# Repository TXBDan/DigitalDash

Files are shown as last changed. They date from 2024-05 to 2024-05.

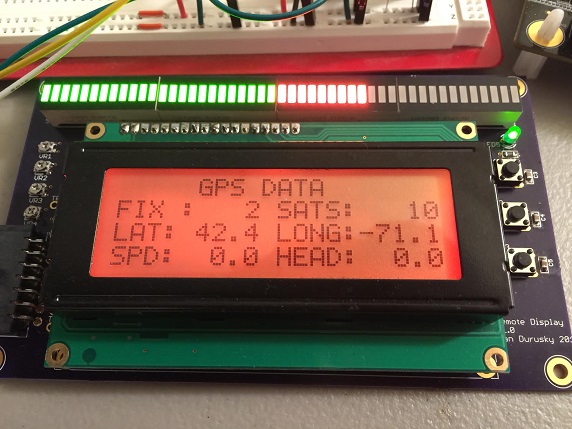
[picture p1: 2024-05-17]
pics/gpspic.jpg

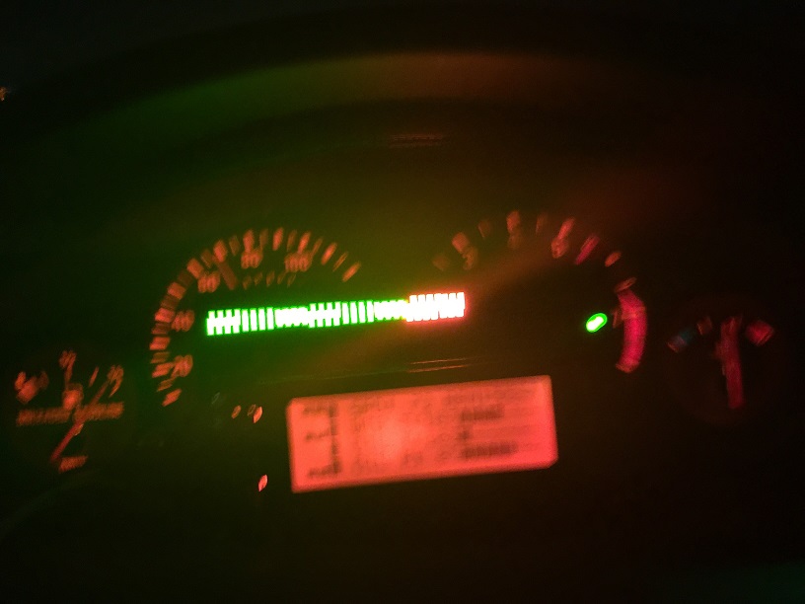
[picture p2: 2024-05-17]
pics/dashnight2.jpg

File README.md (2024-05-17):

# DigitalDash

This is a prototype digital dashboard for use in motorsports. I made it in 2015 and successfully ran it in my track car for a couple years. I'm now archiving the project here.

It features:
* LPC4088 microcontroller
* Many-LED RGB sequential shift light
* 20x4 character LCD display
* 2 LEDs (power/status and alarm)
* 3 push buttons (change screen, select, option)
* 4 analog inputs (water temp, oil temp, oil pressure, throttle position)
* 2 speed/pulse inputs (speed and tach)
* 10Hz GPS (position and elevation)
* 3-axis accelerometer
* SDcard logging

For a lot more info, check out the blog here: https://projectsofdan.com/?cat=18

incar

BlockDiagram

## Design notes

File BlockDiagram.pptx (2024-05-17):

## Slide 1

QSB Baseboard

Main Unit Shield

Dashboard

Shift Light 1-2
HT16K33
I2C1: 0x70

Shift Light 3-4
HT16K33
I2C1: 0x71

20x4 LCD
MCP2300
I2C1: 0x40

Power LED

8chan ADC
MCP3208
SPI1

Pull-up Jumpers

Input Filters

Input Buffers

Temp Sensor
AEM 30-2012

LPC4088
ARM Cortex M4

Temp Sensor
AEM 30-2012

Pressure Sensor
AEM 30-2131-100

Throttle Position
Stock Potentiometer

Trim Pot (R)

Record Button

Trim Pot (G)

Button 1

Accelerometer
MMA7455
I2C1

Vehicle Speed
12V pulse train

Trim Pot (B)

SD Memory Card

Engine Speed
12V pulse train

Trim Pot (Contrast)

Button 2

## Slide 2

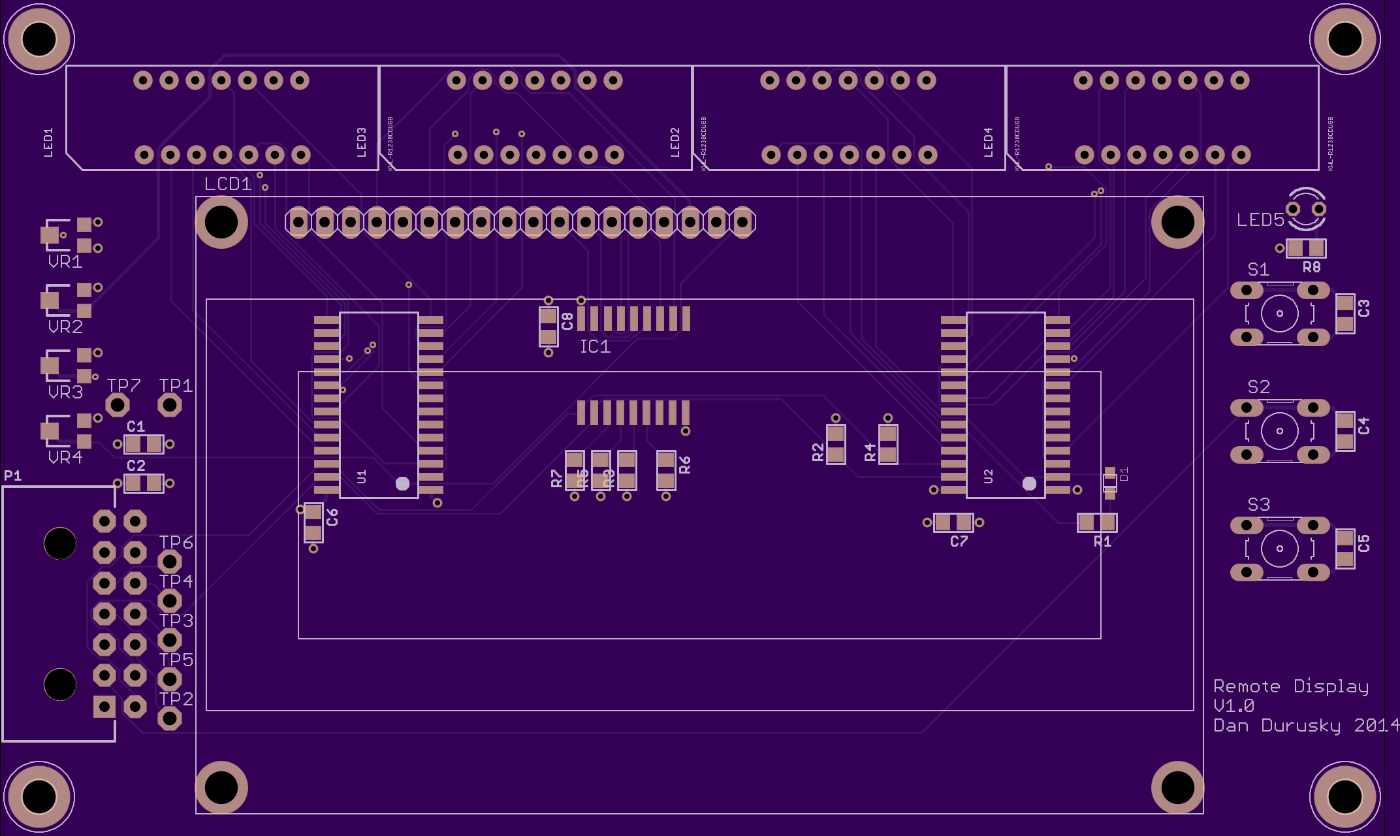
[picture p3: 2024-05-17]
hardware/RemoteDisplay/Layout/top.png

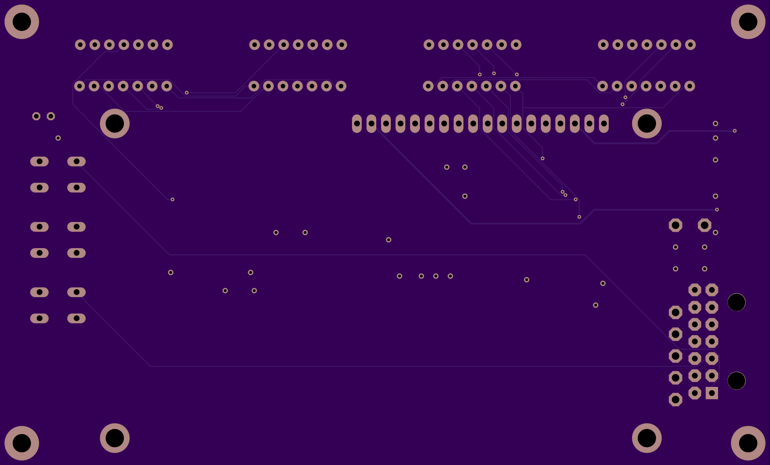
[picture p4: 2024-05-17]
hardware/RemoteDisplay/Layout/bottom.png

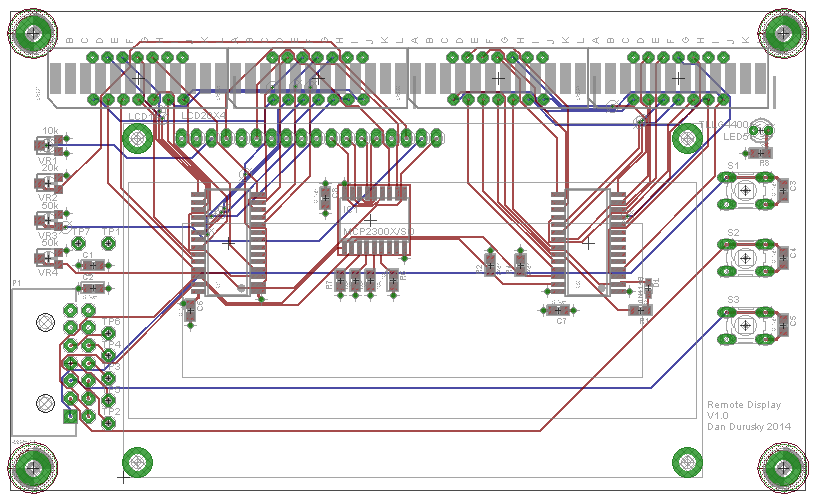
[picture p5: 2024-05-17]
hardware/RemoteDisplay/Layout/Layout.png

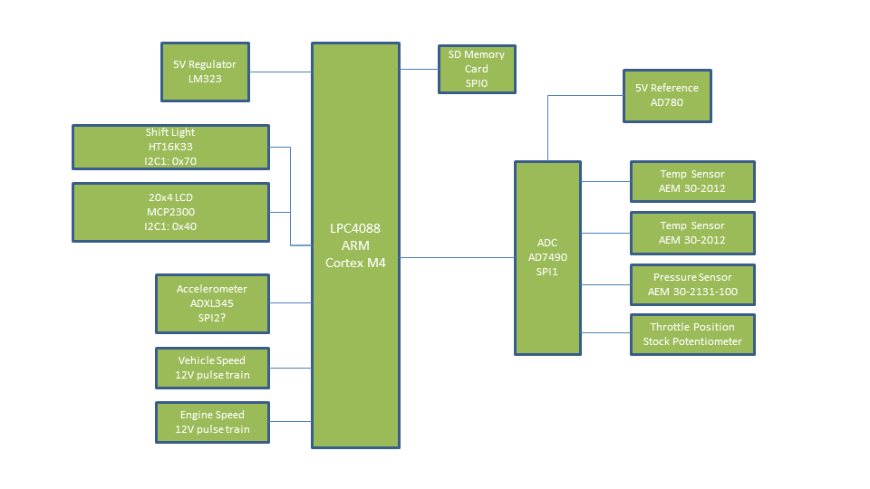
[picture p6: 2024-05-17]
BlockDiagram.png

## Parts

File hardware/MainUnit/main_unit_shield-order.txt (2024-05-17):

Order list for C:/Users/Dan/Documents/eagle/DigitalDash/main_unit_shield.sch					
Exported from EAGLE with DesignLink					
					
Quantity	Value	Package	Manufacturer	Manuf. PN	Description
11	0.1uF	C0805	TDK	C2012X7R1H104K085AA	"TDK - C2012X7R1H104K085AA - CERAMIC CAPACITOR, 0.1UF, 50V, X7R, 0805"
3	10uF	C0805	TDK	C2012X5R1E106K125AB	"TDK - C2012X5R1E106K125AB - CERAMIC CAPACITOR, 10UF, 25V, X5R, 0805"
4		JP1	3M	969102-0000-DA	"3M - 969102-0000-DA - SHUNT, 2POS, 2.54MM"
1	43045-24	43045-24	MOLEX	43045-2400	"MOLEX - 43045-2400 - PLUG & SOCKET CONNECTOR, HEADER, 24POS, 3MM"
1	43045-14	43045-14	MOLEX	43045-1400	"MOLEX - 43045-1400 - PLUG & SOCKET CONNECTOR, HEADER, 14POS, 3MM"
50			Molex	462350001	CONN SOCKET 20-24AWG GOLD
2	20k	R0805	VISHAY/DALE	CRCW080520K0FKEA	"VISHAY DALE - CRCW080520K0FKEA - THICK FILM RESISTOR, 20KOHM, 125mW, 1%"
14	2K2	R0805	VISHAY/DALE	CRCW08052K20FKEA	"VISHAY DALE - CRCW08052K20FKEA - THICK FILM RESISTOR, 2.2KOHM, 125mW, 1%"
2	8k2	R0805	VISHAY/DALE	CRCW08058K20FKEAHP	"VISHAY DRALORIC - CRCW08058K20FKEAHP - RESISTOR, POWER, 0805, 1%, 8K20"
3		SO14	MICROCHIP	MCP6044-E/SL	"MICROCHIP - MCP6044-E/SL - IC, OP-AMP, 14kHZ, 0.003V/ us, 3mV, SOIC14"
1		SO16	MICROCHIP	MCP3208-BI/SL	"MICROCHIP - MCP3208-BI/SL - IC, ADC 12BIT 100kSPS SERIAL SPI SOIC-16"

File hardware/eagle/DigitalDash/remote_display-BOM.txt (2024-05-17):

Order list for C:/Users/Dan/Documents/eagle/DigitalDash/remote_display.sch
Exported from EAGLE with DesignLink

Quantity	Value	Package	Order code	Manufacturer	Manuf. Code	Availability	Price (from)	Description
1	10uF	C0805	04X3278		C2012X5R1E106K125AB	8292	0.229	TDK - C2012X5R1E106K125AB - CERAMIC CAPACITOR, 10UF, 25V, X5R, 0805
7	0.1uF	C0805	04X3288		C2012X7R1H104K085AA	2978	0.016	TDK - C2012X7R1H104K085AA - CERAMIC CAPACITOR, 0.1UF, 50V, X7R, 0805
1	1N4148	SOD-323F	10N9478		MMBT2222ALT3G	4288	0.025	ON SEMICONDUCTOR - MMBT2222ALT3G - BIPOLAR TRANSISTOR, NPN, 40V SOT-23
4	MOUNT-PAD-ROUND3.2	3,2-PAD	unknown					
1	MCP2300X/SO	SO18W	08J8738	MICROCHIP	MCP23008-E/SO	305	0.78	MICROCHIP - MCP23008-E/SO - IC, I/O EXPANDER, 8BIT, 1.7MHZ, SOIC-18
1	LCD20X4	LCD20X4	unknown					
4	KWL-R1230CDUGB	SEGMENT_BICOL_BL-AR12Z3010	unknown					
1	TLLG4400	LED3MM	58K2496	VISHAY/TELEFUNKEN	TLLG4400	29708	0.095	VISHAY SEMICONDUCTOR - TLLG4400 - LED, GREEN, T-1 (3MM), 1.2MCD, 575NM
1	43045-14	43045-14	55R8852		43045-1400	471	2.1	MOLEX - 43045-1400 - PLUG & SOCKET CONNECTOR, HEADER, 14POS, 3MM
1	47k	R0805	41R4787		CRCW080547K0FKEAHP	4329	0.049	VISHAY DRALORIC - CRCW080547K0FKEAHP - RESISTOR, POWER, 0805, 1%, 47K0
2	DNP	R0805	05F1511	VISHAY/DALE	CRCW080510K0FKTA	6001	0.021	VISHAY DALE - CRCW080510K0FKTA - THICK FILM RESISTOR, 10KOHM, 125mW, 1%
4	10k	R0805	05F1511	VISHAY/DALE	CRCW080510K0FKTA	6001	0.021	VISHAY DALE - CRCW080510K0FKTA - THICK FILM RESISTOR, 10KOHM, 125mW, 1%
1	1K2	R0805	05F1511	VISHAY/DALE	CRCW080510K0FKTA	6001	0.021	VISHAY DALE - CRCW080510K0FKTA - THICK FILM RESISTOR, 10KOHM, 125mW, 1%
3		B3F-10XX	unknown		B3F-1000			
7	TPSPAD1-13	P1-13	unknown					
2		SOP28_300MIL	unknown					
1	10k	TC33X	60H9648	BOURNS, INC.	TC33X-2-103E	7500	0.094	BOURNS - TC33X-2-103E - TRIMMER POTENTIOMETER 10KOHM 1TURN, FULL REEL
1	20k	TC33X	97M3839		TC33X-2-203E	0		BOURNS - TC33X-2-203E - TRIMMER POTENTIOMETER 20KOHM -000TURN SMD
2	50k	TC33X	97M3841		TC33X-2-503E	4443	0.113	BOURNS - TC33X-2-503E - TRIMMER POTENTIOMETER 50KOHM -000TURN SMD

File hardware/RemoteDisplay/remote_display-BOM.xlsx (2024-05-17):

Order list for C:/Users/Dan/Documents/eagle/DigitalDash/remote_display.sch
Exported from EAGLE with DesignLink
Quantity | Value | Package | Manufacturer | Manuf. PN | Description
1 | 10uF | C0805 | TDK | C2012X5R1E106K125AB | TDK - C2012X5R1E106K125AB - CERAMIC CAPACITOR, 10UF, 25V, X5R, 0805
7 | 0.1uF | C0805 | TDK | C2012X7R1H104K085AA | TDK - C2012X7R1H104K085AA - CERAMIC CAPACITOR, 0.1UF, 50V, X7R, 0805
1 | 1N4148 | SOD-323F | On Semi | MMBT2222ALT3G | BIPOLAR TRANSISTOR, NPN, 40V SOT-23
1 | MCP2300X/SO | SO18W | MICROCHIP | MCP23008-E/SO | MICROCHIP - MCP23008-E/SO - IC, I/O EXPANDER, 8BIT, 1.7MHZ, SOIC-18
1 | LCD20X4 | LCD20X4 | Adafruit | 499 | Adafruit RGB 20x4 LCD
4 | KWL-R1230CDUGB | SEGMENT_BICOL_BL-AR12Z3010 | Adafruit | KWL-R1230CDUGB | 12bar LED
1 | TLLG4400 | LED3MM | VISHAY/TELEFUNKEN | TLLG4400 | VISHAY SEMICONDUCTOR - TLLG4400 - LED, GREEN, T-1 (3MM), 1.2MCD, 575NM
1 |  | 43045-14 | Molex | 43045-1400 | MOLEX - 43045-1400 - PLUG & SOCKET CONNECTOR, HEADER, 14POS, 3MM
20 |  |  | Molex | 462350001 | CONN SOCKET 20-24AWG GOLD
1 | 47k | R0805 | VISHAY | CRCW080547K0FKEAHP | VISHAY DRALORIC - CRCW080547K0FKEAHP - RESISTOR, POWER, 0805, 1%, 47K0
2 | DNP | R0805 | VISHAY | CRCW080510K0FKTA | VISHAY DALE - CRCW080510K0FKTA - THICK FILM RESISTOR, 10KOHM, 125mW, 1%
4 | 10k | R0805 | VISHAY | CRCW080510K0FKTA | VISHAY DALE - CRCW080510K0FKTA - THICK FILM RESISTOR, 10KOHM, 125mW, 1%
1 | 1K2 | R0805 | VISHAY | CRCW080510K0FKTA | VISHAY DALE - CRCW080510K0FKTA - THICK FILM RESISTOR, 10KOHM, 125mW, 1%
3 |  | B3F-10XX | Omron | B3F-1000 | tactile button switch 6mm
2 |  | SOP28_300MIL | Holtek | HTK1633 | SOIC-28 RAM Mapping 16*8 LED Controller Driver
1 | 10k | TC33X | BOURNS, INC. | TC33X-2-103E | BOURNS - TC33X-2-103E - TRIMMER POTENTIOMETER 10KOHM 1TURN, FULL REEL
1 | 20k | TC33X | BOURNS, INC. | TC33X-2-203E | BOURNS - TC33X-2-203E - TRIMMER POTENTIOMETER 20KOHM -000TURN SMD
2 | 50k | TC33X | BOURNS, INC. | TC33X-2-503E | BOURNS - TC33X-2-503E - TRIMMER POTENTIOMETER 50KOHM -000TURN SMD

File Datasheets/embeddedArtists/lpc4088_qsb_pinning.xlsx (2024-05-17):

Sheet: All pins
Pin Functionality | Pin Name | Edge connector pins | Display connector pins | Xbee connector pins | Usage | Comments
P0[0] / CAN_RD_1 / U3_TXD / I2C1_SDA / U0_TXD | p0_0 | 9
P0[1] / CAN_TD_1 / U3_RXD / I2C1_SCL / U0_RXD | p0_1 | 10
P0[2] / U0_TXD / U3_TXD | p0_2 | 42 |  |  | HDK UART0 TX
P0[3] / U0_RXD / U3_RXD | p0_3 | 41 |  |  | HDK UART0 RX
P0[4] / I2S_RX_SCK / CAN_RD_2 / T2_CAP_0 / unused / CMP_ROSC / unused / LCD_VD_0 | p0_4 | 34 | 1 |  | LCD_VD0 | Only used for 24-bit color depth
P0[5] / I2S_RX_WS / CAN_TD_2 / T2_CAP_1 / unused / CMP_RESET / unused / LCD_VD_1 | p0_5 | 33 | 2 |  | LCD_VD1 | Only used for 24-bit color depth
P0[6] / I2S_RX_SDA / SSP1_SSEL / T2_MAT_0 / U1_RTS / CMP_ROSC / unused / LCD_VD_8 | p0_6 | 14 | 16 |  | LCD_VD8 | Only used for 24-bit color depth
P0[7] / I2S_TX_SCK / SSP1_SCK / T2_MAT_1 / RTC_EV0 / CMP_VREF / unused / LCD_VD_9 | p0_7 | 13 | 17 |  | LCD_VD9 | Only used for 24-bit color depth
P0[8] / I2S_TX_WS / SSP1_MISO / T2_MAT_2 / RTC_EV1 / CMP1_IN3 / unused / LCD_VD_16 | p0_8 | 12 | 29 |  | LCD_VD16 | Only used for 24-bit color depth
P0[9] / I2S_TX_SDA / SSP1_MOSI / T2_MAT_3 / RTC_EV2 / CMP1_IN2 / unused / LCD_VD_17 | p0_9 | 11 | 30 |  | LCD_VD17 | Only used for 24-bit color depth
P0[10] / U2_TXD / I2C2_SDA / T3_MAT_0 / unused / unused / unused / LCD_VD_5 | p0_10 |  | 10 |  | LCD_VD5
P0[11] / U2_RXD / I2C2_SCL / T3_MAT_1 / unused / unused / unused / LCD_VD_10 | p0_11 |  | 18 |  | LCD_VD10
P0[13] / USB_UP_LED2 / SSP1_MOSI / ADC0_IN[7] | p0_13 |  |  |  | Controls mbed LED#2
P0[19] / U1_DSR / SD_CLK / I2C1_SDA / unused / unused / unused / LCD_VD_13 | p0_19 |  | 24 |  | LCD_VD13
P0[20] / U1_DTR / SD_CMD / I2C1_SCL / unused / unused / unused / LCD_VD_14 | p0_20 |  | 26 |  | LCD_VD14
P0[21] / U1_RI / SD_PWR / U4_OE / CAN_RD_1 / U4_CLK | p0_21 | 8
P0[23] / ADC0_IN[0] / I2S_RX_SCK / T3_CAP_0 | p0_23 | 15
P0[24] / ADC0_IN[1] / I2S_RX_WS / T3_CAP_1 | p0_24 | 16
P0[25] / ADC0_IN[2] / I2S_RX_SDA / U3_TXD | p0_25 | 17
P0[26] / ADC0_IN[3] / DAC_OUT / U3_RXD | p0_26 | 18
P0[27] / I2C0_SDA / USB_SDA1 | p0_27 |  | 54 |  | LCD I2C interface (I2C#0)
P0[28] / I2C0_SCL / USB_SCL1 | p0_28 |  | 55 |  | LCD I2C interface (I2C#0)
P0[29] / USB_D+1 / EINT_0 | p0_29 |  |  |  | USB Host interface
P0[30] / USB_D-1 / EINT_1 | p0_30 |  |  |  | USB Host interface
P0[31] / USB_D+2 | p0_31 | 35 |  |  | USB Device or external interface
USB_D-2 | usb_dm2 | 36 |  |  | USB Device or external interface
P1[2] / ENET_TXD[2] / SD_CLK / PWM0_1 | p1_2 | 30
P1[3] / ENET_TXD[3] / SD_CMD / PWM0_2 | p1_3 | 29
P1[5] / ENET_TX_ER / SD_PWR / PWM0_3 / CMP1_IN1 | p1_5 | 28
P1[6] / ENET_TX_CLK / SD_DAT_0 / PWM0_4 / CMP0_IN3 | p1_6 | 27
P1[7] / ENET_COL / SD_DAT_1 / PWM0_5 / CMP1_IN0 | p1_7 | 26
P1[11] / ENET_RXD_2 / SD_DAT_2 / PWM0_6 | p1_11 | 25
P1[12] / ENET_RXD_3 / SD_DAT_3 / PWM0_CAP_0 / CMP1_OUT | p1_12 | 24
P1[13] / ENET_RX_DV | p1_13 |  |  |  | Controls mbed LED#3
P1[18] / USB_UP_LED1 / PWM1_1 / T1_CAP_0 / unused / SSP1_MISO | p1_18 |  |  |  | Controls mbed LED#1
P1[20] / USB_TX_DP1 / PWM1_2 / QEI_PHA / MC_FB0 / SSP0_SCK / LCD_VD_6 / LCD_VD_10 | p1_20 | 7 |  |  |  | Note that SPI0 is also used by LCD interface
P1[21] / USB_TX_DM1 / PWM1_3 / SSP0_SSEL / MC_ABORTn / unused / LCD_VD_7 / LCD_VD_11 | p1_21 |  | 20 |  | LCD_VD11
P1[22] / USB_RCV1 / USB_PWRD1 / T1_MAT_0 / MC_0B / SSP1_MOSI / LCD_VD_8 / LCD_VD_12 | p1_22 |  | 22 |  | LCD_VD12
P1[23] / USB_RX_DP1 / PWM1_4 / QEI_PHB / MC_FB1 / SSP0_MISO / LCD_VD_9 / LCD_VD_13 | p1_23 | 6 |  |  |  | Note that SPI0 is also used by LCD interface
P1[24] / USB_RX_DM1 / PWM1_5 / QEI_IDX / MC_FB2 / SSP0_MOSI / LCD_VD_10 / LCD_VD_14 | p1_24 | 5 |  |  |  | Note that SPI0 is also used by LCD interface
P1[25] / USB_LS1n / USB_HSTEN1n / T1_MAT_1 / MC_1A / CLKOUT / LCD_VD_11 / LCD_VD_15 | p1_25 |  | 28 |  | LCD_VD15
P1[26] / USB_SSPND1n / PWM1_6 / T0_CAP_0 / MC_1B / SSP1_SSEL / LCD_VD_12 / LCD_VD_20 | p1_26 |  | 36 |  | LCD_VD20
P1[27] / USB_INT1n / USB_OVRCR1n / T0_CAP_1 / CLKOUT / unused / LCD_VD_13 / LCD_VD_21 | p1_27 |  | 38 |  | LCD_VD21
P1[28] / USB_SCL1 / PWM1_CAP_0 / T0_MAT_0 / MC_2A / SSP0_SSEL / LCD_VD_14 / LCD_VD_22 | p1_28 |  | 40 |  | LCD_VD22
P1[29] / USB_SDA1 / PWM1_CAP_1 / T0_MAT_1 / MC_2B / U4_TXD / LCD_VD_15 / LCD_VD_23 | p1_29 |  | 42 |  | LCD_VD23
P1[30] / USB_PWRD2 / USB_VBUS / ADC0_IN[4] / I2C0_SDA / U3_OE | p1_30 | 19
P1[31] / USB_OVRCR2n / SSP1_SCK / ADC0_IN[5] / I2C0_SCL | p1_31 | 20
P2[0] / PWM1_1 / U1_TXD / unused / unused / unused / unused / LCD_PWR | p2_0 |  | 49 |  | LCD PWR
P2[1] / PWM1_2 / U1_RXD / unused / unused / unused / unused / LCD_LE | p2_1 |  | 53 |  | LCD LE
P2[2] / PWM1_3 / U1_CTS / T2_MAT_3 / unused / TRACEDATA[3] / unused / LCD_DCLK | p2_2 |  | 46 |  | LCD DCLK | Also used for trace data3
P2[3] / PWM1_4 / U1_DCD / T2_MAT_2 / unused / TRACEDATA[2] / unused / LCD_FP | p2_3 |  | 50 |  | LCD VSYNC | Also used for trace data2
P2[4] / PWM1_5 / U1_DSR / T2_MAT_1 / unused / TRACEDATA[1] / unused / LCD_ENAB_M | p2_4 |  | 48 |  | LCD DNAB | Also used for trace data1
P2[5] / PWM1_6 / U1_DTR / T2_MAT_0 / unused / TRACEDATA[0] / unused / LCD_LP | p2_5 |  | 52 |  | LCD HSYNC | Also used for trace data0
P2[6] / PWM1_CAP_0 / U1_RI / T2_CAP_0 / U2_OE / TRACECLK / LCD_VD_0 / LCD_VD_4 | p2_6 |  | 8 |  | LCD_VD4 | Also used for trace clock
P2[8] / CAN_TD_2 / U2_TXD / U1_CTS / ENET_MDC / unused / LCD_VD_2 / LCD_VD_6 | p2_8 |  | 12 |  | LCD_VD6
P2[9] / USB_CONNECT1 / U2_RXD / U4_RXD / ENET_MDIO / unused / LCD_VD_3 / LCD_VD_7 | p2_9 |  | 14 |  | LCD_VD7
P2[10] / EINT_0 / NMI | p2_10 | 23 |  |  |  | Must not be pulled low at reset, will enable ISP
P2[11] / EINT_1 / SD_DAT_1 / I2S_TX_SCK / unused / unused / unused / LCD_CLKIN | p2_11 |  | 44 |  | LCD CLKIN
P2[12] / EINT_2 / SD_DAT_2 / I2S_TX_WS / LCD_VD_4 / LCD_VD_3 / LCD_VD_8 / LCD_VD_18 | p2_12 |  | 32 |  | LCD_VD18
P2[13] / EINT_3 / SD_DAT_3 / I2S_TX_SDA / unused / LCD_VD_5 / LCD_VD_9 / LCD_VD_19 | p2_13 |  | 34 |  | LCD_VD19
P2[19] / EMC_CLK[1] | p2_19 |  |  |  | Controls mbed LED#4
P2[21] / EMC_DYCSn[1] | p2_21 |  | 60 |  | LCD GPIO
P2[22] / EMC_DYCSn[2] / SSP0_SCK / T3_CAP_0 | p2_22 |  | 56 |  | LCD SPI-SCK, using SPI0 | Signal can also exist at edge connector pin 7
P2[23] / EMC_DYCSn[3] / SSP0_SSEL / T3_CAP_1 | p2_23 |  | 57 |  | LCD SPI-SSEL,using SPI0
P2[25] / EMC_CKE[1] | p2_25 |  | 61 |  | LCD GPIO
P2[26] / EMC_CKE[2] / SSP0_MISO / T3_MAT_0 | p2_26 |  | 58 |  | LCD SPI-MISO, using SPI0 | Signal can also exist at edge connector pin 6
P2[27] / EMC_CKE[3] / SSP0_MOSI / T3_MAT_1 | p2_27 |  | 59 |  | LCD SPI-MOSI, using SPI0 | Signal can also exist at edge connector pin 5
P4[17] / EMC_A[17] | p4_17 |  |  | 5 | Xbee RESET
P4[18] / EMC_A[18] | p4_18 |  |  | 4 | Xbee CD/DOUT_EN
P4[19] / EMC_A[19] | p4_19 |  |  | 9 | Xbee DTR/SLEEP_RQ
P4[20] / EMC_A[20] / I2C2_SDA / SSP1_SCK | p4_20 |  |  | 12 | Xbee CTS
P4[21] / EMC_A[21] / I2C2_SCL / SSP1_SSEL | p4_21 |  |  | 16 | Xbee RTS
P4[22] / EMC_A[22] / U2_TXD / SSP1_MISO | p4_22 |  |  | 3 | Xbee DIN, using UART2
P4[23] / EMC_A[23] / U2_RXD / SSP1_MOSI | p4_23 |  |  | 2 | Xbee DOUT, using UART2
P4[28] / EMC_BLSn[2] / U3_TXD / T2_MAT_0 / unused / LCD_VD_6 / LCD_VD_10 / LCD_VD_2 | p4_28 |  | 4 |  | LCD_VD2
P4[29] / EMC_BLSn[3] / U3_RXD / T2_MAT_1 / I2C2_SCL / LCD_VD_7 / LCD_VD_11 / LCD_VD_3 | p4_29 |  | 6 |  | LCD_VD3
P5[0] / EMC_A[24] / SSP2_MOSI / T2_MAT_2 | p5_0 | 39
P5[1] / EMC_A[25] / SSP2_MISO / T2_MAT_3 | p5_1 | 38
P5[2] / EMC_A[26] / SSP2_SCK / T3_MAT_2 / unused / I2C0_SDA | p5_2 | 32 |  |  |  | Note that I2C0 is also used by LCD interface
P5[3] / EMC_A[27] / SSP2_SSEL / unused / U4_RXD / I2C0_SCL | p5_3 | 31 |  |  |  | Note that I2C0 is also used by LCD interface
P5[4] / U0_OE / unused / T3_MAT_3 / U4_TXD | p5_4 | 37
RESETn | resetn | 4
RTC_ALARM | rtc_alarm | 40
Vbat | vbat | 3

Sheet: Edge pins sorted
Pin Functionality | Pin Name | Edge connector pins | Display connector pins | Xbee connector pins | Usage | Comments
Vbat | vbat | 3
RESETn | resetn | 4
P1[24] / USB_RX_DM1 / PWM1_5 / QEI_IDX / MC_FB2 / SSP0_MOSI / LCD_VD_10 / LCD_VD_14 | p1_24 | 5 |  |  |  | Note that SPI0 is also used by LCD interface
P1[23] / USB_RX_DP1 / PWM1_4 / QEI_PHB / MC_FB1 / SSP0_MISO / LCD_VD_9 / LCD_VD_13 | p1_23 | 6 |  |  |  | Note that SPI0 is also used by LCD interface
P1[20] / USB_TX_DP1 / PWM1_2 / QEI_PHA / MC_FB0 / SSP0_SCK / LCD_VD_6 / LCD_VD_10 | p1_20 | 7 |  |  |  | Note that SPI0 is also used by LCD interface
P0[21] / U1_RI / SD_PWR / U4_OE / CAN_RD_1 / U4_CLK | p0_21 | 8
P0[0] / CAN_RD_1 / U3_TXD / I2C1_SDA / U0_TXD | p0_0 | 9
P0[1] / CAN_TD_1 / U3_RXD / I2C1_SCL / U0_RXD | p0_1 | 10
P0[9] / I2S_TX_SDA / SSP1_MOSI / T2_MAT_3 / RTC_EV2 / CMP1_IN2 / unused / LCD_VD_17 | p0_9 | 11 | 30 |  | LCD_VD17 | Only used for 24-bit color depth
P0[8] / I2S_TX_WS / SSP1_MISO / T2_MAT_2 / RTC_EV1 / CMP1_IN3 / unused / LCD_VD_16 | p0_8 | 12 | 29 |  | LCD_VD16 | Only used for 24-bit color depth
P0[7] / I2S_TX_SCK / SSP1_SCK / T2_MAT_1 / RTC_EV0 / CMP_VREF / unused / LCD_VD_9 | p0_7 | 13 | 17 |  | LCD_VD9 | Only used for 24-bit color depth
P0[6] / I2S_RX_SDA / SSP1_SSEL / T2_MAT_0 / U1_RTS / CMP_ROSC / unused / LCD_VD_8 | p0_6 | 14 | 16 |  | LCD_VD8 | Only used for 24-bit color depth
P0[23] / ADC0_IN[0] / I2S_RX_SCK / T3_CAP_0 | p0_23 | 15
P0[24] / ADC0_IN[1] / I2S_RX_WS / T3_CAP_1 | p0_24 | 16
P0[25] / ADC0_IN[2] / I2S_RX_SDA / U3_TXD | p0_25 | 17
P0[26] / ADC0_IN[3] / DAC_OUT / U3_RXD | p0_26 | 18
P1[30] / USB_PWRD2 / USB_VBUS / ADC0_IN[4] / I2C0_SDA / U3_OE | p1_30 | 19
P1[31] / USB_OVRCR2n / SSP1_SCK / ADC0_IN[5] / I2C0_SCL | p1_31 | 20
P2[10] / EINT_0 / NMI | p2_10 | 23 |  |  |  | Must not be pulled low at reset, will enable ISP
P1[12] / ENET_RXD_3 / SD_DAT_3 / PWM0_CAP_0 / CMP1_OUT | p1_12 | 24
P1[11] / ENET_RXD_2 / SD_DAT_2 / PWM0_6 | p1_11 | 25
P1[7] / ENET_COL / SD_DAT_1 / PWM0_5 / CMP1_IN0 | p1_7 | 26
P1[6] / ENET_TX_CLK / SD_DAT_0 / PWM0_4 / CMP0_IN3 | p1_6 | 27
P1[5] / ENET_TX_ER / SD_PWR / PWM0_3 / CMP1_IN1 | p1_5 | 28
P1[3] / ENET_TXD[3] / SD_CMD / PWM0_2 | p1_3 | 29
P1[2] / ENET_TXD[2] / SD_CLK / PWM0_1 | p1_2 | 30
P5[3] / EMC_A[27] / SSP2_SSEL / unused / U4_RXD / I2C0_SCL | p5_3 | 31 |  |  |  | Note that I2C0 is also used by LCD interface
P5[2] / EMC_A[26] / SSP2_SCK / T3_MAT_2 / unused / I2C0_SDA | p5_2 | 32 |  |  |  | Note that I2C0 is also used by LCD interface
P0[5] / I2S_RX_WS / CAN_TD_2 / T2_CAP_1 / unused / CMP_RESET / unused / LCD_VD_1 | p0_5 | 33 | 2 |  | LCD_VD1 | Only used for 24-bit color depth
P0[4] / I2S_RX_SCK / CAN_RD_2 / T2_CAP_0 / unused / CMP_ROSC / unused / LCD_VD_0 | p0_4 | 34 | 1 |  | LCD_VD0 | Only used for 24-bit color depth
P0[31] / USB_D+2 | p0_31 | 35 |  |  | USB Device or external interface
USB_D-2 | usb_dm2 | 36 |  |  | USB Device or external interface
P5[4] / U0_OE / unused / T3_MAT_3 / U4_TXD | p5_4 | 37
P5[1] / EMC_A[25] / SSP2_MISO / T2_MAT_3 | p5_1 | 38
P5[0] / EMC_A[24] / SSP2_MOSI / T2_MAT_2 | p5_0 | 39
RTC_ALARM | rtc_alarm | 40
P0[3] / U0_RXD / U3_RXD | p0_3 | 41 |  |  | HDK UART RX
P0[2] / U0_TXD / U3_TXD | p0_2 | 42 |  |  | HDK UART TX
P0[10] / U2_TXD / I2C2_SDA / T3_MAT_0 / unused / unused / unused / LCD_VD_5 | p0_10 |  | 10 |  | LCD_VD5
P0[11] / U2_RXD / I2C2_SCL / T3_MAT_1 / unused / unused / unused / LCD_VD_10 | p0_11 |  | 18 |  | LCD_VD10
P0[13] / USB_UP_LED2 / SSP1_MOSI / ADC0_IN[7] | p0_13 |  |  |  | Controls mbed LED#2
P0[19] / U1_DSR / SD_CLK / I2C1_SDA / unused / unused / unused / LCD_VD_13 | p0_19 |  | 24 |  | LCD_VD13
P0[20] / U1_DTR / SD_CMD / I2C1_SCL / unused / unused / unused / LCD_VD_14 | p0_20 |  | 26 |  | LCD_VD14
P0[27] / I2C0_SDA / USB_SDA1 | p0_27 |  | 54 |  | LCD I2C interface (I2C#0)
P0[28] / I2C0_SCL / USB_SCL1 | p0_28 |  | 55 |  | LCD I2C interface (I2C#0)
P0[29] / USB_D+1 / EINT_0 | p0_29 |  |  |  | USB Host interface
P0[30] / USB_D-1 / EINT_1 | p0_30 |  |  |  | USB Host interface
P1[13] / ENET_RX_DV | p1_13 |  |  |  | Controls mbed LED#3
P1[18] / USB_UP_LED1 / PWM1_1 / T1_CAP_0 / unused / SSP1_MISO | p1_18 |  |  |  | Controls mbed LED#1
P1[21] / USB_TX_DM1 / PWM1_3 / SSP0_SSEL / MC_ABORTn / unused / LCD_VD_7 / LCD_VD_11 | p1_21 |  | 20 |  | LCD_VD11
P1[22] / USB_RCV1 / USB_PWRD1 / T1_MAT_0 / MC_0B / SSP1_MOSI / LCD_VD_8 / LCD_VD_12 | p1_22 |  | 22 |  | LCD_VD12
P1[25] / USB_LS1n / USB_HSTEN1n / T1_MAT_1 / MC_1A / CLKOUT / LCD_VD_11 / LCD_VD_15 | p1_25 |  | 28 |  | LCD_VD15
P1[26] / USB_SSPND1n / PWM1_6 / T0_CAP_0 / MC_1B / SSP1_SSEL / LCD_VD_12 / LCD_VD_20 | p1_26 |  | 36 |  | LCD_VD20
P1[27] / USB_INT1n / USB_OVRCR1n / T0_CAP_1 / CLKOUT / unused / LCD_VD_13 / LCD_VD_21 | p1_27 |  | 38 |  | LCD_VD21
P1[28] / USB_SCL1 / PWM1_CAP_0 / T0_MAT_0 / MC_2A / SSP0_SSEL / LCD_VD_14 / LCD_VD_22 | p1_28 |  | 40 |  | LCD_VD22
P1[29] / USB_SDA1 / PWM1_CAP_1 / T0_MAT_1 / MC_2B / U4_TXD / LCD_VD_15 / LCD_VD_23 | p1_29 |  | 42 |  | LCD_VD23
P2[0] / PWM1_1 / U1_TXD / unused / unused / unused / unused / LCD_PWR | p2_0 |  | 49 |  | LCD PWR
P2[1] / PWM1_2 / U1_RXD / unused / unused / unused / unused / LCD_LE | p2_1 |  | 53 |  | LCD LE
P2[2] / PWM1_3 / U1_CTS / T2_MAT_3 / unused / TRACEDATA[3] / unused / LCD_DCLK | p2_2 |  | 46 |  | LCD DCLK | Also used for trace data3
P2[3] / PWM1_4 / U1_DCD / T2_MAT_2 / unused / TRACEDATA[2] / unused / LCD_FP | p2_3 |  | 50 |  | LCD VSYNC | Also used for trace data2
P2[4] / PWM1_5 / U1_DSR / T2_MAT_1 / unused / TRACEDATA[1] / unused / LCD_ENAB_M | p2_4 |  | 48 |  | LCD DNAB | Also used for trace data1
P2[5] / PWM1_6 / U1_DTR / T2_MAT_0 / unused / TRACEDATA[0] / unused / LCD_LP | p2_5 |  | 52 |  | LCD HSYNC | Also used for trace data0
P2[6] / PWM1_CAP_0 / U1_RI / T2_CAP_0 / U2_OE / TRACECLK / LCD_VD_0 / LCD_VD_4 | p2_6 |  | 8 |  | LCD_VD4 | Also used for trace clock
P2[8] / CAN_TD_2 / U2_TXD / U1_CTS / ENET_MDC / unused / LCD_VD_2 / LCD_VD_6 | p2_8 |  | 12 |  | LCD_VD6
P2[9] / USB_CONNECT1 / U2_RXD / U4_RXD / ENET_MDIO / unused / LCD_VD_3 / LCD_VD_7 | p2_9 |  | 14 |  | LCD_VD7
P2[11] / EINT_1 / SD_DAT_1 / I2S_TX_SCK / unused / unused / unused / LCD_CLKIN | p2_11 |  | 44 |  | LCD CLKIN
P2[12] / EINT_2 / SD_DAT_2 / I2S_TX_WS / LCD_VD_4 / LCD_VD_3 / LCD_VD_8 / LCD_VD_18 | p2_12 |  | 32 |  | LCD_VD18
P2[13] / EINT_3 / SD_DAT_3 / I2S_TX_SDA / unused / LCD_VD_5 / LCD_VD_9 / LCD_VD_19 | p2_13 |  | 34 |  | LCD_VD19
P2[19] / EMC_CLK[1] | p2_19 |  |  |  | Controls mbed LED#4
P2[21] / EMC_DYCSn[1] | p2_21 |  | 60 |  | LCD GPIO
P2[22] / EMC_DYCSn[2] / SSP0_SCK / T3_CAP_0 | p2_22 |  | 56 |  | LCD SPI-SCK, using SPI0 | Signal can also exist at edge connector pin 7
P2[23] / EMC_DYCSn[3] / SSP0_SSEL / T3_CAP_1 | p2_23 |  | 57 |  | LCD SPI-SSEL,using SPI0
P2[25] / EMC_CKE[1] | p2_25 |  | 61 |  | LCD GPIO
P2[26] / EMC_CKE[2] / SSP0_MISO / T3_MAT_0 | p2_26 |  | 58 |  | LCD SPI-MISO, using SPI0 | Signal can also exist at edge connector pin 6
P2[27] / EMC_CKE[3] / SSP0_MOSI / T3_MAT_1 | p2_27 |  | 59 |  | LCD SPI-MOSI, using SPI0 | Signal can also exist at edge connector pin 5
P4[17] / EMC_A[17] | p4_17 |  |  | 5 | Xbee RESET
P4[18] / EMC_A[18] | p4_18 |  |  | 4 | Xbee CD/DOUT_EN
P4[19] / EMC_A[19] | p4_19 |  |  | 9 | Xbee DTR/SLEEP_RQ
P4[20] / EMC_A[20] / I2C2_SDA / SSP1_SCK | p4_20 |  |  | 12 | Xbee CTS
P4[21] / EMC_A[21] / I2C2_SCL / SSP1_SSEL | p4_21 |  |  | 16 | Xbee RTS
P4[22] / EMC_A[22] / U2_TXD / SSP1_MISO | p4_22 |  |  | 3 | Xbee DIN, using UART2
P4[23] / EMC_A[23] / U2_RXD / SSP1_MOSI | p4_23 |  |  | 2 | Xbee DOUT, using UART2
P4[28] / EMC_BLSn[2] / U3_TXD / T2_MAT_0 / unused / LCD_VD_6 / LCD_VD_10 / LCD_VD_2 | p4_28 |  | 4 |  | LCD_VD2
P4[29] / EMC_BLSn[3] / U3_RXD / T2_MAT_1 / I2C2_SCL / LCD_VD_7 / LCD_VD_11 / LCD_VD_3 | p4_29 |  | 6 |  | LCD_VD3

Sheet: LCD pins sorted
Pin Functionality | Pin Name | Edge connector pins | Display connector pins | Xbee connector pins | Usage | Comments
P0[4] / I2S_RX_SCK / CAN_RD_2 / T2_CAP_0 / unused / CMP_ROSC / unused / LCD_VD_0 | p0_4 | 34 | 1 |  | LCD_VD0 | Only used for 24-bit color depth
P0[5] / I2S_RX_WS / CAN_TD_2 / T2_CAP_1 / unused / CMP_RESET / unused / LCD_VD_1 | p0_5 | 33 | 2 |  | LCD_VD1 | Only used for 24-bit color depth
P4[28] / EMC_BLSn[2] / U3_TXD / T2_MAT_0 / unused / LCD_VD_6 / LCD_VD_10 / LCD_VD_2 | p4_28 |  | 4 |  | LCD_VD2
P4[29] / EMC_BLSn[3] / U3_RXD / T2_MAT_1 / I2C2_SCL / LCD_VD_7 / LCD_VD_11 / LCD_VD_3 | p4_29 |  | 6 |  | LCD_VD3
P2[6] / PWM1_CAP_0 / U1_RI / T2_CAP_0 / U2_OE / TRACECLK / LCD_VD_0 / LCD_VD_4 | p2_6 |  | 8 |  | LCD_VD4 | Also used for trace clock
P0[10] / U2_TXD / I2C2_SDA / T3_MAT_0 / unused / unused / unused / LCD_VD_5 | p0_10 |  | 10 |  | LCD_VD5
P2[8] / CAN_TD_2 / U2_TXD / U1_CTS / ENET_MDC / unused / LCD_VD_2 / LCD_VD_6 | p2_8 |  | 12 |  | LCD_VD6
P2[9] / USB_CONNECT1 / U2_RXD / U4_RXD / ENET_MDIO / unused / LCD_VD_3 / LCD_VD_7 | p2_9 |  | 14 |  | LCD_VD7
P0[6] / I2S_RX_SDA / SSP1_SSEL / T2_MAT_0 / U1_RTS / CMP_ROSC / unused / LCD_VD_8 | p0_6 | 14 | 16 |  | LCD_VD8 | Only used for 24-bit color depth
P0[7] / I2S_TX_SCK / SSP1_SCK / T2_MAT_1 / RTC_EV0 / CMP_VREF / unused / LCD_VD_9 | p0_7 | 13 | 17 |  | LCD_VD9 | Only used for 24-bit color depth
P0[11] / U2_RXD / I2C2_SCL / T3_MAT_1 / unused / unused / unused / LCD_VD_10 | p0_11 |  | 18 |  | LCD_VD10
P1[21] / USB_TX_DM1 / PWM1_3 / SSP0_SSEL / MC_ABORTn / unused / LCD_VD_7 / LCD_VD_11 | p1_21 |  | 20 |  | LCD_VD11
P1[22] / USB_RCV1 / USB_PWRD1 / T1_MAT_0 / MC_0B / SSP1_MOSI / LCD_VD_8 / LCD_VD_12 | p1_22 |  | 22 |  | LCD_VD12
P0[19] / U1_DSR / SD_CLK / I2C1_SDA / unused / unused / unused / LCD_VD_13 | p0_19 |  | 24 |  | LCD_VD13
P0[20] / U1_DTR / SD_CMD / I2C1_SCL / unused / unused / unused / LCD_VD_14 | p0_20 |  | 26 |  | LCD_VD14
P1[25] / USB_LS1n / USB_HSTEN1n / T1_MAT_1 / MC_1A / CLKOUT / LCD_VD_11 / LCD_VD_15 | p1_25 |  | 28 |  | LCD_VD15
P0[8] / I2S_TX_WS / SSP1_MISO / T2_MAT_2 / RTC_EV1 / CMP1_IN3 / unused / LCD_VD_16 | p0_8 | 12 | 29 |  | LCD_VD16 | Only used for 24-bit color depth
P0[9] / I2S_TX_SDA / SSP1_MOSI / T2_MAT_3 / RTC_EV2 / CMP1_IN2 / unused / LCD_VD_17 | p0_9 | 11 | 30 |  | LCD_VD17 | Only used for 24-bit color depth
P2[12] / EINT_2 / SD_DAT_2 / I2S_TX_WS / LCD_VD_4 / LCD_VD_3 / LCD_VD_8 / LCD_VD_18 | p2_12 |  | 32 |  | LCD_VD18
P2[13] / EINT_3 / SD_DAT_3 / I2S_TX_SDA / unused / LCD_VD_5 / LCD_VD_9 / LCD_VD_19 | p2_13 |  | 34 |  | LCD_VD19
P1[26] / USB_SSPND1n / PWM1_6 / T0_CAP_0 / MC_1B / SSP1_SSEL / LCD_VD_12 / LCD_VD_20 | p1_26 |  | 36 |  | LCD_VD20
P1[27] / USB_INT1n / USB_OVRCR1n / T0_CAP_1 / CLKOUT / unused / LCD_VD_13 / LCD_VD_21 | p1_27 |  | 38 |  | LCD_VD21
P1[28] / USB_SCL1 / PWM1_CAP_0 / T0_MAT_0 / MC_2A / SSP0_SSEL / LCD_VD_14 / LCD_VD_22 | p1_28 |  | 40 |  | LCD_VD22
P1[29] / USB_SDA1 / PWM1_CAP_1 / T0_MAT_1 / MC_2B / U4_TXD / LCD_VD_15 / LCD_VD_23 | p1_29 |  | 42 |  | LCD_VD23
P2[11] / EINT_1 / SD_DAT_1 / I2S_TX_SCK / unused / unused / unused / LCD_CLKIN | p2_11 |  | 44 |  | LCD CLKIN
P2[2] / PWM1_3 / U1_CTS / T2_MAT_3 / unused / TRACEDATA[3] / unused / LCD_DCLK | p2_2 |  | 46 |  | LCD DCLK | Also used for trace data3
P2[4] / PWM1_5 / U1_DSR / T2_MAT_1 / unused / TRACEDATA[1] / unused / LCD_ENAB_M | p2_4 |  | 48 |  | LCD DNAB | Also used for trace data1
P2[0] / PWM1_1 / U1_TXD / unused / unused / unused / unused / LCD_PWR | p2_0 |  | 49 |  | LCD PWR
P2[3] / PWM1_4 / U1_DCD / T2_MAT_2 / unused / TRACEDATA[2] / unused / LCD_FP | p2_3 |  | 50 |  | LCD VSYNC | Also used for trace data2
P2[5] / PWM1_6 / U1_DTR / T2_MAT_0 / unused / TRACEDATA[0] / unused / LCD_LP | p2_5 |  | 52 |  | LCD HSYNC | Also used for trace data0
P2[1] / PWM1_2 / U1_RXD / unused / unused / unused / unused / LCD_LE | p2_1 |  | 53 |  | LCD LE
P0[27] / I2C0_SDA / USB_SDA1 | p0_27 |  | 54 |  | LCD I2C interface (I2C#0)
P0[28] / I2C0_SCL / USB_SCL1 | p0_28 |  | 55 |  | LCD I2C interface (I2C#0)
P2[22] / EMC_DYCSn[2] / SSP0_SCK / T3_CAP_0 | p2_22 |  | 56 |  | LCD SPI-SCK, using SPI0 | Signal can also exist at edge connector pin 7
P2[23] / EMC_DYCSn[3] / SSP0_SSEL / T3_CAP_1 | p2_23 |  | 57 |  | LCD SPI-SSEL,using SPI0
P2[26] / EMC_CKE[2] / SSP0_MISO / T3_MAT_0 | p2_26 |  | 58 |  | LCD SPI-MISO, using SPI0 | Signal can also exist at edge connector pin 6
P2[27] / EMC_CKE[3] / SSP0_MOSI / T3_MAT_1 | p2_27 |  | 59 |  | LCD SPI-MOSI, using SPI0 | Signal can also exist at edge connector pin 5
P2[21] / EMC_DYCSn[1] | p2_21 |  | 60 |  | LCD GPIO
P2[25] / EMC_CKE[1] | p2_25 |  | 61 |  | LCD GPIO
P0[0] / CAN_RD_1 / U3_TXD / I2C1_SDA / U0_TXD | p0_0 | 9
P0[1] / CAN_TD_1 / U3_RXD / I2C1_SCL / U0_RXD | p0_1 | 10
P0[2] / U0_TXD / U3_TXD | p0_2 | 42 |  |  | HDK UART TX
P0[3] / U0_RXD / U3_RXD | p0_3 | 41 |  |  | HDK UART RX
P0[13] / USB_UP_LED2 / SSP1_MOSI / ADC0_IN[7] | p0_13 |  |  |  | Controls mbed LED#2
P0[21] / U1_RI / SD_PWR / U4_OE / CAN_RD_1 / U4_CLK | p0_21 | 8
P0[23] / ADC0_IN[0] / I2S_RX_SCK / T3_CAP_0 | p0_23 | 15
P0[24] / ADC0_IN[1] / I2S_RX_WS / T3_CAP_1 | p0_24 | 16
P0[25] / ADC0_IN[2] / I2S_RX_SDA / U3_TXD | p0_25 | 17
P0[26] / ADC0_IN[3] / DAC_OUT / U3_RXD | p0_26 | 18
P0[29] / USB_D+1 / EINT_0 | p0_29 |  |  |  | USB Host interface
P0[30] / USB_D-1 / EINT_1 | p0_30 |  |  |  | USB Host interface
P0[31] / USB_D+2 | p0_31 | 35 |  |  | USB Device or external interface
USB_D-2 | usb_dm2 | 36 |  |  | USB Device or external interface
P1[2] / ENET_TXD[2] / SD_CLK / PWM0_1 | p1_2 | 30
P1[3] / ENET_TXD[3] / SD_CMD / PWM0_2 | p1_3 | 29
P1[5] / ENET_TX_ER / SD_PWR / PWM0_3 / CMP1_IN1 | p1_5 | 28
P1[6] / ENET_TX_CLK / SD_DAT_0 / PWM0_4 / CMP0_IN3 | p1_6 | 27
P1[7] / ENET_COL / SD_DAT_1 / PWM0_5 / CMP1_IN0 | p1_7 | 26
P1[11] / ENET_RXD_2 / SD_DAT_2 / PWM0_6 | p1_11 | 25
P1[12] / ENET_RXD_3 / SD_DAT_3 / PWM0_CAP_0 / CMP1_OUT | p1_12 | 24
P1[13] / ENET_RX_DV | p1_13 |  |  |  | Controls mbed LED#3
P1[18] / USB_UP_LED1 / PWM1_1 / T1_CAP_0 / unused / SSP1_MISO | p1_18 |  |  |  | Controls mbed LED#1
P1[20] / USB_TX_DP1 / PWM1_2 / QEI_PHA / MC_FB0 / SSP0_SCK / LCD_VD_6 / LCD_VD_10 | p1_20 | 7 |  |  |  | Note that SPI0 is also used by LCD interface
P1[23] / USB_RX_DP1 / PWM1_4 / QEI_PHB / MC_FB1 / SSP0_MISO / LCD_VD_9 / LCD_VD_13 | p1_23 | 6 |  |  |  | Note that SPI0 is also used by LCD interface
P1[24] / USB_RX_DM1 / PWM1_5 / QEI_IDX / MC_FB2 / SSP0_MOSI / LCD_VD_10 / LCD_VD_14 | p1_24 | 5 |  |  |  | Note that SPI0 is also used by LCD interface
P1[30] / USB_PWRD2 / USB_VBUS / ADC0_IN[4] / I2C0_SDA / U3_OE | p1_30 | 19
P1[31] / USB_OVRCR2n / SSP1_SCK / ADC0_IN[5] / I2C0_SCL | p1_31 | 20
P2[10] / EINT_0 / NMI | p2_10 | 23 |  |  |  | Must not be pulled low at reset, will enable ISP
P2[19] / EMC_CLK[1] | p2_19 |  |  |  | Controls mbed LED#4
P4[17] / EMC_A[17] | p4_17 |  |  | 5 | Xbee RESET
P4[18] / EMC_A[18] | p4_18 |  |  | 4 | Xbee CD/DOUT_EN
P4[19] / EMC_A[19] | p4_19 |  |  | 9 | Xbee DTR/SLEEP_RQ
P4[20] / EMC_A[20] / I2C2_SDA / SSP1_SCK | p4_20 |  |  | 12 | Xbee CTS
P4[21] / EMC_A[21] / I2C2_SCL / SSP1_SSEL | p4_21 |  |  | 16 | Xbee RTS
P4[22] / EMC_A[22] / U2_TXD / SSP1_MISO | p4_22 |  |  | 3 | Xbee DIN, using UART2
P4[23] / EMC_A[23] / U2_RXD / SSP1_MOSI | p4_23 |  |  | 2 | Xbee DOUT, using UART2
P5[0] / EMC_A[24] / SSP2_MOSI / T2_MAT_2 | p5_0 | 39
P5[1] / EMC_A[25] / SSP2_MISO / T2_MAT_3 | p5_1 | 38
P5[2] / EMC_A[26] / SSP2_SCK / T3_MAT_2 / unused / I2C0_SDA | p5_2 | 32 |  |  |  | Note that I2C0 is also used by LCD interface
P5[3] / EMC_A[27] / SSP2_SSEL / unused / U4_RXD / I2C0_SCL | p5_3 | 31 |  |  |  | Note that I2C0 is also used by LCD interface
P5[4] / U0_OE / unused / T3_MAT_3 / U4_TXD | p5_4 | 37
RESETn | resetn | 4
RTC_ALARM | rtc_alarm | 40
Vbat | vbat | 3

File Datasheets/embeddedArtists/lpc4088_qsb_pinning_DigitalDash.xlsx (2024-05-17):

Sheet: All pins
Pin Functionality | Pin Name | Digital Dashboard | Edge connector pins | Display connector pins | Xbee connector pins | Usage | Comments
Vbat | vbat |  | 3
RESETn | resetn |  | 4
P1[24] / USB_RX_DM1 / PWM1_5 / QEI_IDX / MC_FB2 / SSP0_MOSI / LCD_VD_10 / LCD_VD_14 | p1_24 | potential LCD | 5 |  |  |  | Note that SPI0 is also used by LCD interface
P1[23] / USB_RX_DP1 / PWM1_4 / QEI_PHB / MC_FB1 / SSP0_MISO / LCD_VD_9 / LCD_VD_13 | p1_23 | potential LCD | 6 |  |  |  | Note that SPI0 is also used by LCD interface
P1[20] / USB_TX_DP1 / PWM1_2 / QEI_PHA / MC_FB0 / SSP0_SCK / LCD_VD_6 / LCD_VD_10 | p1_20 | potential LCD | 7 |  |  |  | Note that SPI0 is also used by LCD interface
P0[21] / U1_RI / SD_PWR / U4_OE / CAN_RD_1 / U4_CLK | p0_21 | ADC /CS | 8
P0[0] / CAN_RD_1 / U3_TXD / I2C1_SDA / U0_TXD | p0_0 | I2C1 | 9
P0[1] / CAN_TD_1 / U3_RXD / I2C1_SCL / U0_RXD | p0_1 | I2C1 | 10
P0[9] / I2S_TX_SDA / SSP1_MOSI / T2_MAT_3 / RTC_EV2 / CMP1_IN2 / unused / LCD_VD_17 | p0_9 | SPI1: ADC | 11 | 30 |  | LCD_VD17 | Only used for 24-bit color depth
P0[8] / I2S_TX_WS / SSP1_MISO / T2_MAT_2 / RTC_EV1 / CMP1_IN3 / unused / LCD_VD_16 | p0_8 | SPI1: ADC | 12 | 29 |  | LCD_VD16 | Only used for 24-bit color depth
P0[7] / I2S_TX_SCK / SSP1_SCK / T2_MAT_1 / RTC_EV0 / CMP_VREF / unused / LCD_VD_9 | p0_7 | SPI1: ADC | 13 | 17 |  | LCD_VD9 | Only used for 24-bit color depth
P0[6] / I2S_RX_SDA / SSP1_SSEL / T2_MAT_0 / U1_RTS / CMP_ROSC / unused / LCD_VD_8 | p0_6 | Interrupt, tach input | 14 | 16 |  | LCD_VD8 | Only used for 24-bit color depth
P0[23] / ADC0_IN[0] / I2S_RX_SCK / T3_CAP_0 | p0_23 | Interrupt, vehicle speed input | 15
P0[24] / ADC0_IN[1] / I2S_RX_WS / T3_CAP_1 | p0_24 | Record button | 16
P0[25] / ADC0_IN[2] / I2S_RX_SDA / U3_TXD | p0_25 | button #1 | 17
P0[26] / ADC0_IN[3] / DAC_OUT / U3_RXD | p0_26 | button #2 | 18
P1[30] / USB_PWRD2 / USB_VBUS / ADC0_IN[4] / I2C0_SDA / U3_OE | p1_30 |  | 19
P1[31] / USB_OVRCR2n / SSP1_SCK / ADC0_IN[5] / I2C0_SCL | p1_31 |  | 20
P2[10] / EINT_0 / NMI | p2_10 |  | 23 |  |  |  | Must not be pulled low at reset, will enable ISP
P1[12] / ENET_RXD_3 / SD_DAT_3 / PWM0_CAP_0 / CMP1_OUT | p1_12 | SD Card | 24
P1[11] / ENET_RXD_2 / SD_DAT_2 / PWM0_6 | p1_11 | SD Card | 25
P1[7] / ENET_COL / SD_DAT_1 / PWM0_5 / CMP1_IN0 | p1_7 | SD Card | 26
P1[6] / ENET_TX_CLK / SD_DAT_0 / PWM0_4 / CMP0_IN3 | p1_6 | SD Card | 27
P1[5] / ENET_TX_ER / SD_PWR / PWM0_3 / CMP1_IN1 | p1_5 | SD Card | 28
P1[3] / ENET_TXD[3] / SD_CMD / PWM0_2 | p1_3 | SD Card | 29
P1[2] / ENET_TXD[2] / SD_CLK / PWM0_1 | p1_2 | SD Card | 30
P5[3] / EMC_A[27] / SSP2_SSEL / unused / U4_RXD / I2C0_SCL | p5_3 |  | 31 |  |  |  | Note that I2C0 is also used by LCD interface
P5[2] / EMC_A[26] / SSP2_SCK / T3_MAT_2 / unused / I2C0_SDA | p5_2 | SPI2 - accelerometer | 32 |  |  |  | Note that I2C0 is also used by LCD interface
P0[5] / I2S_RX_WS / CAN_TD_2 / T2_CAP_1 / unused / CMP_RESET / unused / LCD_VD_1 | p0_5 | SD Card - CD | 33 | 2 |  | LCD_VD1 | Only used for 24-bit color depth
P0[4] / I2S_RX_SCK / CAN_RD_2 / T2_CAP_0 / unused / CMP_ROSC / unused / LCD_VD_0 | p0_4 |  | 34 | 1 |  | LCD_VD0 | Only used for 24-bit color depth
P0[31] / USB_D+2 | p0_31 |  | 35 |  |  | USB Device or external interface
USB_D-2 | usb_dm2 |  | 36 |  |  | USB Device or external interface
P5[4] / U0_OE / unused / T3_MAT_3 / U4_TXD | p5_4 |  | 37
P5[1] / EMC_A[25] / SSP2_MISO / T2_MAT_3 | p5_1 | SPI2 - accelerometer | 38
P5[0] / EMC_A[24] / SSP2_MOSI / T2_MAT_2 | p5_0 | SPI2 - accelerometer | 39
RTC_ALARM | rtc_alarm |  | 40
P0[3] / U0_RXD / U3_RXD | p0_3 |  | 41 |  |  | HDK UART0 RX
P0[2] / U0_TXD / U3_TXD | p0_2 |  | 42 |  |  | HDK UART0 TX
P0[10] / U2_TXD / I2C2_SDA / T3_MAT_0 / unused / unused / unused / LCD_VD_5 | p0_10 |  |  | 10 |  | LCD_VD5
P0[11] / U2_RXD / I2C2_SCL / T3_MAT_1 / unused / unused / unused / LCD_VD_10 | p0_11 |  |  | 18 |  | LCD_VD10
P0[13] / USB_UP_LED2 / SSP1_MOSI / ADC0_IN[7] | p0_13 |  |  |  |  | Controls mbed LED#2
P0[19] / U1_DSR / SD_CLK / I2C1_SDA / unused / unused / unused / LCD_VD_13 | p0_19 |  |  | 24 |  | LCD_VD13
P0[20] / U1_DTR / SD_CMD / I2C1_SCL / unused / unused / unused / LCD_VD_14 | p0_20 |  |  | 26 |  | LCD_VD14
P0[27] / I2C0_SDA / USB_SDA1 | p0_27 |  |  | 54 |  | LCD I2C interface (I2C#0)
P0[28] / I2C0_SCL / USB_SCL1 | p0_28 |  |  | 55 |  | LCD I2C interface (I2C#0)
P0[29] / USB_D+1 / EINT_0 | p0_29 |  |  |  |  | USB Host interface
P0[30] / USB_D-1 / EINT_1 | p0_30 |  |  |  |  | USB Host interface
P1[13] / ENET_RX_DV | p1_13 |  |  |  |  | Controls mbed LED#3
P1[18] / USB_UP_LED1 / PWM1_1 / T1_CAP_0 / unused / SSP1_MISO | p1_18 |  |  |  |  | Controls mbed LED#1
P1[21] / USB_TX_DM1 / PWM1_3 / SSP0_SSEL / MC_ABORTn / unused / LCD_VD_7 / LCD_VD_11 | p1_21 |  |  | 20 |  | LCD_VD11
P1[22] / USB_RCV1 / USB_PWRD1 / T1_MAT_0 / MC_0B / SSP1_MOSI / LCD_VD_8 / LCD_VD_12 | p1_22 |  |  | 22 |  | LCD_VD12
P1[25] / USB_LS1n / USB_HSTEN1n / T1_MAT_1 / MC_1A / CLKOUT / LCD_VD_11 / LCD_VD_15 | p1_25 |  |  | 28 |  | LCD_VD15
P1[26] / USB_SSPND1n / PWM1_6 / T0_CAP_0 / MC_1B / SSP1_SSEL / LCD_VD_12 / LCD_VD_20 | p1_26 |  |  | 36 |  | LCD_VD20
P1[27] / USB_INT1n / USB_OVRCR1n / T0_CAP_1 / CLKOUT / unused / LCD_VD_13 / LCD_VD_21 | p1_27 |  |  | 38 |  | LCD_VD21
P1[28] / USB_SCL1 / PWM1_CAP_0 / T0_MAT_0 / MC_2A / SSP0_SSEL / LCD_VD_14 / LCD_VD_22 | p1_28 |  |  | 40 |  | LCD_VD22
P1[29] / USB_SDA1 / PWM1_CAP_1 / T0_MAT_1 / MC_2B / U4_TXD / LCD_VD_15 / LCD_VD_23 | p1_29 |  |  | 42 |  | LCD_VD23
P2[0] / PWM1_1 / U1_TXD / unused / unused / unused / unused / LCD_PWR | p2_0 |  |  | 49 |  | LCD PWR
P2[1] / PWM1_2 / U1_RXD / unused / unused / unused / unused / LCD_LE | p2_1 |  |  | 53 |  | LCD LE
P2[2] / PWM1_3 / U1_CTS / T2_MAT_3 / unused / TRACEDATA[3] / unused / LCD_DCLK | p2_2 |  |  | 46 |  | LCD DCLK | Also used for trace data3
P2[3] / PWM1_4 / U1_DCD / T2_MAT_2 / unused / TRACEDATA[2] / unused / LCD_FP | p2_3 |  |  | 50 |  | LCD VSYNC | Also used for trace data2
P2[4] / PWM1_5 / U1_DSR / T2_MAT_1 / unused / TRACEDATA[1] / unused / LCD_ENAB_M | p2_4 |  |  | 48 |  | LCD DNAB | Also used for trace data1
P2[5] / PWM1_6 / U1_DTR / T2_MAT_0 / unused / TRACEDATA[0] / unused / LCD_LP | p2_5 |  |  | 52 |  | LCD HSYNC | Also used for trace data0
P2[6] / PWM1_CAP_0 / U1_RI / T2_CAP_0 / U2_OE / TRACECLK / LCD_VD_0 / LCD_VD_4 | p2_6 |  |  | 8 |  | LCD_VD4 | Also used for trace clock
P2[8] / CAN_TD_2 / U2_TXD / U1_CTS / ENET_MDC / unused / LCD_VD_2 / LCD_VD_6 | p2_8 |  |  | 12 |  | LCD_VD6
P2[9] / USB_CONNECT1 / U2_RXD / U4_RXD / ENET_MDIO / unused / LCD_VD_3 / LCD_VD_7 | p2_9 |  |  | 14 |  | LCD_VD7
P2[11] / EINT_1 / SD_DAT_1 / I2S_TX_SCK / unused / unused / unused / LCD_CLKIN | p2_11 |  |  | 44 |  | LCD CLKIN
P2[12] / EINT_2 / SD_DAT_2 / I2S_TX_WS / LCD_VD_4 / LCD_VD_3 / LCD_VD_8 / LCD_VD_18 | p2_12 |  |  | 32 |  | LCD_VD18
P2[13] / EINT_3 / SD_DAT_3 / I2S_TX_SDA / unused / LCD_VD_5 / LCD_VD_9 / LCD_VD_19 | p2_13 |  |  | 34 |  | LCD_VD19
P2[19] / EMC_CLK[1] | p2_19 |  |  |  |  | Controls mbed LED#4
P2[21] / EMC_DYCSn[1] | p2_21 |  |  | 60 |  | LCD GPIO
P2[22] / EMC_DYCSn[2] / SSP0_SCK / T3_CAP_0 | p2_22 |  |  | 56 |  | LCD SPI-SCK, using SPI0 | Signal can also exist at edge connector pin 7
P2[23] / EMC_DYCSn[3] / SSP0_SSEL / T3_CAP_1 | p2_23 |  |  | 57 |  | LCD SPI-SSEL,using SPI0
P2[25] / EMC_CKE[1] | p2_25 |  |  | 61 |  | LCD GPIO
P2[26] / EMC_CKE[2] / SSP0_MISO / T3_MAT_0 | p2_26 |  |  | 58 |  | LCD SPI-MISO, using SPI0 | Signal can also exist at edge connector pin 6
P2[27] / EMC_CKE[3] / SSP0_MOSI / T3_MAT_1 | p2_27 |  |  | 59 |  | LCD SPI-MOSI, using SPI0 | Signal can also exist at edge connector pin 5
P4[17] / EMC_A[17] | p4_17 |  |  |  | 5 | Xbee RESET
P4[18] / EMC_A[18] | p4_18 |  |  |  | 4 | Xbee CD/DOUT_EN
P4[19] / EMC_A[19] | p4_19 |  |  |  | 9 | Xbee DTR/SLEEP_RQ
P4[20] / EMC_A[20] / I2C2_SDA / SSP1_SCK | p4_20 |  |  |  | 12 | Xbee CTS
P4[21] / EMC_A[21] / I2C2_SCL / SSP1_SSEL | p4_21 |  |  |  | 16 | Xbee RTS
P4[22] / EMC_A[22] / U2_TXD / SSP1_MISO | p4_22 | GPS uart |  |  | 3 | Xbee DIN, using UART2
P4[23] / EMC_A[23] / U2_RXD / SSP1_MOSI | p4_23 | GPS uart |  |  | 2 | Xbee DOUT, using UART2
P4[28] / EMC_BLSn[2] / U3_TXD / T2_MAT_0 / unused / LCD_VD_6 / LCD_VD_10 / LCD_VD_2 | p4_28 |  |  | 4 |  | LCD_VD2
P4[29] / EMC_BLSn[3] / U3_RXD / T2_MAT_1 / I2C2_SCL / LCD_VD_7 / LCD_VD_11 / LCD_VD_3 | p4_29 |  |  | 6 |  | LCD_VD3

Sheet: Edge pins sorted
Pin Functionality | Pin Name | Edge connector pins | Display connector pins | Xbee connector pins | Usage | Comments
Vbat | vbat | 3
RESETn | resetn | 4
P1[24] / USB_RX_DM1 / PWM1_5 / QEI_IDX / MC_FB2 / SSP0_MOSI / LCD_VD_10 / LCD_VD_14 | p1_24 | 5 |  |  |  | Note that SPI0 is also used by LCD interface
P1[23] / USB_RX_DP1 / PWM1_4 / QEI_PHB / MC_FB1 / SSP0_MISO / LCD_VD_9 / LCD_VD_13 | p1_23 | 6 |  |  |  | Note that SPI0 is also used by LCD interface
P1[20] / USB_TX_DP1 / PWM1_2 / QEI_PHA / MC_FB0 / SSP0_SCK / LCD_VD_6 / LCD_VD_10 | p1_20 | 7 |  |  |  | Note that SPI0 is also used by LCD interface
P0[21] / U1_RI / SD_PWR / U4_OE / CAN_RD_1 / U4_CLK | p0_21 | 8
P0[0] / CAN_RD_1 / U3_TXD / I2C1_SDA / U0_TXD | p0_0 | 9
P0[1] / CAN_TD_1 / U3_RXD / I2C1_SCL / U0_RXD | p0_1 | 10
P0[9] / I2S_TX_SDA / SSP1_MOSI / T2_MAT_3 / RTC_EV2 / CMP1_IN2 / unused / LCD_VD_17 | p0_9 | 11 | 30 |  | LCD_VD17 | Only used for 24-bit color depth
P0[8] / I2S_TX_WS / SSP1_MISO / T2_MAT_2 / RTC_EV1 / CMP1_IN3 / unused / LCD_VD_16 | p0_8 | 12 | 29 |  | LCD_VD16 | Only used for 24-bit color depth
P0[7] / I2S_TX_SCK / SSP1_SCK / T2_MAT_1 / RTC_EV0 / CMP_VREF / unused / LCD_VD_9 | p0_7 | 13 | 17 |  | LCD_VD9 | Only used for 24-bit color depth
P0[6] / I2S_RX_SDA / SSP1_SSEL / T2_MAT_0 / U1_RTS / CMP_ROSC / unused / LCD_VD_8 | p0_6 | 14 | 16 |  | LCD_VD8 | Only used for 24-bit color depth
P0[23] / ADC0_IN[0] / I2S_RX_SCK / T3_CAP_0 | p0_23 | 15
P0[24] / ADC0_IN[1] / I2S_RX_WS / T3_CAP_1 | p0_24 | 16
P0[25] / ADC0_IN[2] / I2S_RX_SDA / U3_TXD | p0_25 | 17
P0[26] / ADC0_IN[3] / DAC_OUT / U3_RXD | p0_26 | 18
P1[30] / USB_PWRD2 / USB_VBUS / ADC0_IN[4] / I2C0_SDA / U3_OE | p1_30 | 19
P1[31] / USB_OVRCR2n / SSP1_SCK / ADC0_IN[5] / I2C0_SCL | p1_31 | 20
P2[10] / EINT_0 / NMI | p2_10 | 23 |  |  |  | Must not be pulled low at reset, will enable ISP
P1[12] / ENET_RXD_3 / SD_DAT_3 / PWM0_CAP_0 / CMP1_OUT | p1_12 | 24
P1[11] / ENET_RXD_2 / SD_DAT_2 / PWM0_6 | p1_11 | 25
P1[7] / ENET_COL / SD_DAT_1 / PWM0_5 / CMP1_IN0 | p1_7 | 26
P1[6] / ENET_TX_CLK / SD_DAT_0 / PWM0_4 / CMP0_IN3 | p1_6 | 27
P1[5] / ENET_TX_ER / SD_PWR / PWM0_3 / CMP1_IN1 | p1_5 | 28
P1[3] / ENET_TXD[3] / SD_CMD / PWM0_2 | p1_3 | 29
P1[2] / ENET_TXD[2] / SD_CLK / PWM0_1 | p1_2 | 30
P5[3] / EMC_A[27] / SSP2_SSEL / unused / U4_RXD / I2C0_SCL | p5_3 | 31 |  |  |  | Note that I2C0 is also used by LCD interface
P5[2] / EMC_A[26] / SSP2_SCK / T3_MAT_2 / unused / I2C0_SDA | p5_2 | 32 |  |  |  | Note that I2C0 is also used by LCD interface
P0[5] / I2S_RX_WS / CAN_TD_2 / T2_CAP_1 / unused / CMP_RESET / unused / LCD_VD_1 | p0_5 | 33 | 2 |  | LCD_VD1 | Only used for 24-bit color depth
P0[4] / I2S_RX_SCK / CAN_RD_2 / T2_CAP_0 / unused / CMP_ROSC / unused / LCD_VD_0 | p0_4 | 34 | 1 |  | LCD_VD0 | Only used for 24-bit color depth
P0[31] / USB_D+2 | p0_31 | 35 |  |  | USB Device or external interface
USB_D-2 | usb_dm2 | 36 |  |  | USB Device or external interface
P5[4] / U0_OE / unused / T3_MAT_3 / U4_TXD | p5_4 | 37
P5[1] / EMC_A[25] / SSP2_MISO / T2_MAT_3 | p5_1 | 38
P5[0] / EMC_A[24] / SSP2_MOSI / T2_MAT_2 | p5_0 | 39
RTC_ALARM | rtc_alarm | 40
P0[3] / U0_RXD / U3_RXD | p0_3 | 41 |  |  | HDK UART RX
P0[2] / U0_TXD / U3_TXD | p0_2 | 42 |  |  | HDK UART TX
P0[10] / U2_TXD / I2C2_SDA / T3_MAT_0 / unused / unused / unused / LCD_VD_5 | p0_10 |  | 10 |  | LCD_VD5
P0[11] / U2_RXD / I2C2_SCL / T3_MAT_1 / unused / unused / unused / LCD_VD_10 | p0_11 |  | 18 |  | LCD_VD10
P0[13] / USB_UP_LED2 / SSP1_MOSI / ADC0_IN[7] | p0_13 |  |  |  | Controls mbed LED#2
P0[19] / U1_DSR / SD_CLK / I2C1_SDA / unused / unused / unused / LCD_VD_13 | p0_19 |  | 24 |  | LCD_VD13
P0[20] / U1_DTR / SD_CMD / I2C1_SCL / unused / unused / unused / LCD_VD_14 | p0_20 |  | 26 |  | LCD_VD14
P0[27] / I2C0_SDA / USB_SDA1 | p0_27 |  | 54 |  | LCD I2C interface (I2C#0)
P0[28] / I2C0_SCL / USB_SCL1 | p0_28 |  | 55 |  | LCD I2C interface (I2C#0)
P0[29] / USB_D+1 / EINT_0 | p0_29 |  |  |  | USB Host interface
P0[30] / USB_D-1 / EINT_1 | p0_30 |  |  |  | USB Host interface
P1[13] / ENET_RX_DV | p1_13 |  |  |  | Controls mbed LED#3
P1[18] / USB_UP_LED1 / PWM1_1 / T1_CAP_0 / unused / SSP1_MISO | p1_18 |  |  |  | Controls mbed LED#1
P1[21] / USB_TX_DM1 / PWM1_3 / SSP0_SSEL / MC_ABORTn / unused / LCD_VD_7 / LCD_VD_11 | p1_21 |  | 20 |  | LCD_VD11
P1[22] / USB_RCV1 / USB_PWRD1 / T1_MAT_0 / MC_0B / SSP1_MOSI / LCD_VD_8 / LCD_VD_12 | p1_22 |  | 22 |  | LCD_VD12
P1[25] / USB_LS1n / USB_HSTEN1n / T1_MAT_1 / MC_1A / CLKOUT / LCD_VD_11 / LCD_VD_15 | p1_25 |  | 28 |  | LCD_VD15
P1[26] / USB_SSPND1n / PWM1_6 / T0_CAP_0 / MC_1B / SSP1_SSEL / LCD_VD_12 / LCD_VD_20 | p1_26 |  | 36 |  | LCD_VD20
P1[27] / USB_INT1n / USB_OVRCR1n / T0_CAP_1 / CLKOUT / unused / LCD_VD_13 / LCD_VD_21 | p1_27 |  | 38 |  | LCD_VD21
P1[28] / USB_SCL1 / PWM1_CAP_0 / T0_MAT_0 / MC_2A / SSP0_SSEL / LCD_VD_14 / LCD_VD_22 | p1_28 |  | 40 |  | LCD_VD22
P1[29] / USB_SDA1 / PWM1_CAP_1 / T0_MAT_1 / MC_2B / U4_TXD / LCD_VD_15 / LCD_VD_23 | p1_29 |  | 42 |  | LCD_VD23
P2[0] / PWM1_1 / U1_TXD / unused / unused / unused / unused / LCD_PWR | p2_0 |  | 49 |  | LCD PWR
P2[1] / PWM1_2 / U1_RXD / unused / unused / unused / unused / LCD_LE | p2_1 |  | 53 |  | LCD LE
P2[2] / PWM1_3 / U1_CTS / T2_MAT_3 / unused / TRACEDATA[3] / unused / LCD_DCLK | p2_2 |  | 46 |  | LCD DCLK | Also used for trace data3
P2[3] / PWM1_4 / U1_DCD / T2_MAT_2 / unused / TRACEDATA[2] / unused / LCD_FP | p2_3 |  | 50 |  | LCD VSYNC | Also used for trace data2
P2[4] / PWM1_5 / U1_DSR / T2_MAT_1 / unused / TRACEDATA[1] / unused / LCD_ENAB_M | p2_4 |  | 48 |  | LCD DNAB | Also used for trace data1
P2[5] / PWM1_6 / U1_DTR / T2_MAT_0 / unused / TRACEDATA[0] / unused / LCD_LP | p2_5 |  | 52 |  | LCD HSYNC | Also used for trace data0
P2[6] / PWM1_CAP_0 / U1_RI / T2_CAP_0 / U2_OE / TRACECLK / LCD_VD_0 / LCD_VD_4 | p2_6 |  | 8 |  | LCD_VD4 | Also used for trace clock
P2[8] / CAN_TD_2 / U2_TXD / U1_CTS / ENET_MDC / unused / LCD_VD_2 / LCD_VD_6 | p2_8 |  | 12 |  | LCD_VD6
P2[9] / USB_CONNECT1 / U2_RXD / U4_RXD / ENET_MDIO / unused / LCD_VD_3 / LCD_VD_7 | p2_9 |  | 14 |  | LCD_VD7
P2[11] / EINT_1 / SD_DAT_1 / I2S_TX_SCK / unused / unused / unused / LCD_CLKIN | p2_11 |  | 44 |  | LCD CLKIN
P2[12] / EINT_2 / SD_DAT_2 / I2S_TX_WS / LCD_VD_4 / LCD_VD_3 / LCD_VD_8 / LCD_VD_18 | p2_12 |  | 32 |  | LCD_VD18
P2[13] / EINT_3 / SD_DAT_3 / I2S_TX_SDA / unused / LCD_VD_5 / LCD_VD_9 / LCD_VD_19 | p2_13 |  | 34 |  | LCD_VD19
P2[19] / EMC_CLK[1] | p2_19 |  |  |  | Controls mbed LED#4
P2[21] / EMC_DYCSn[1] | p2_21 |  | 60 |  | LCD GPIO
P2[22] / EMC_DYCSn[2] / SSP0_SCK / T3_CAP_0 | p2_22 |  | 56 |  | LCD SPI-SCK, using SPI0 | Signal can also exist at edge connector pin 7
P2[23] / EMC_DYCSn[3] / SSP0_SSEL / T3_CAP_1 | p2_23 |  | 57 |  | LCD SPI-SSEL,using SPI0
P2[25] / EMC_CKE[1] | p2_25 |  | 61 |  | LCD GPIO
P2[26] / EMC_CKE[2] / SSP0_MISO / T3_MAT_0 | p2_26 |  | 58 |  | LCD SPI-MISO, using SPI0 | Signal can also exist at edge connector pin 6
P2[27] / EMC_CKE[3] / SSP0_MOSI / T3_MAT_1 | p2_27 |  | 59 |  | LCD SPI-MOSI, using SPI0 | Signal can also exist at edge connector pin 5
P4[17] / EMC_A[17] | p4_17 |  |  | 5 | Xbee RESET
P4[18] / EMC_A[18] | p4_18 |  |  | 4 | Xbee CD/DOUT_EN
P4[19] / EMC_A[19] | p4_19 |  |  | 9 | Xbee DTR/SLEEP_RQ
P4[20] / EMC_A[20] / I2C2_SDA / SSP1_SCK | p4_20 |  |  | 12 | Xbee CTS
P4[21] / EMC_A[21] / I2C2_SCL / SSP1_SSEL | p4_21 |  |  | 16 | Xbee RTS
P4[22] / EMC_A[22] / U2_TXD / SSP1_MISO | p4_22 |  |  | 3 | Xbee DIN, using UART2
P4[23] / EMC_A[23] / U2_RXD / SSP1_MOSI | p4_23 |  |  | 2 | Xbee DOUT, using UART2
P4[28] / EMC_BLSn[2] / U3_TXD / T2_MAT_0 / unused / LCD_VD_6 / LCD_VD_10 / LCD_VD_2 | p4_28 |  | 4 |  | LCD_VD2
P4[29] / EMC_BLSn[3] / U3_RXD / T2_MAT_1 / I2C2_SCL / LCD_VD_7 / LCD_VD_11 / LCD_VD_3 | p4_29 |  | 6 |  | LCD_VD3
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

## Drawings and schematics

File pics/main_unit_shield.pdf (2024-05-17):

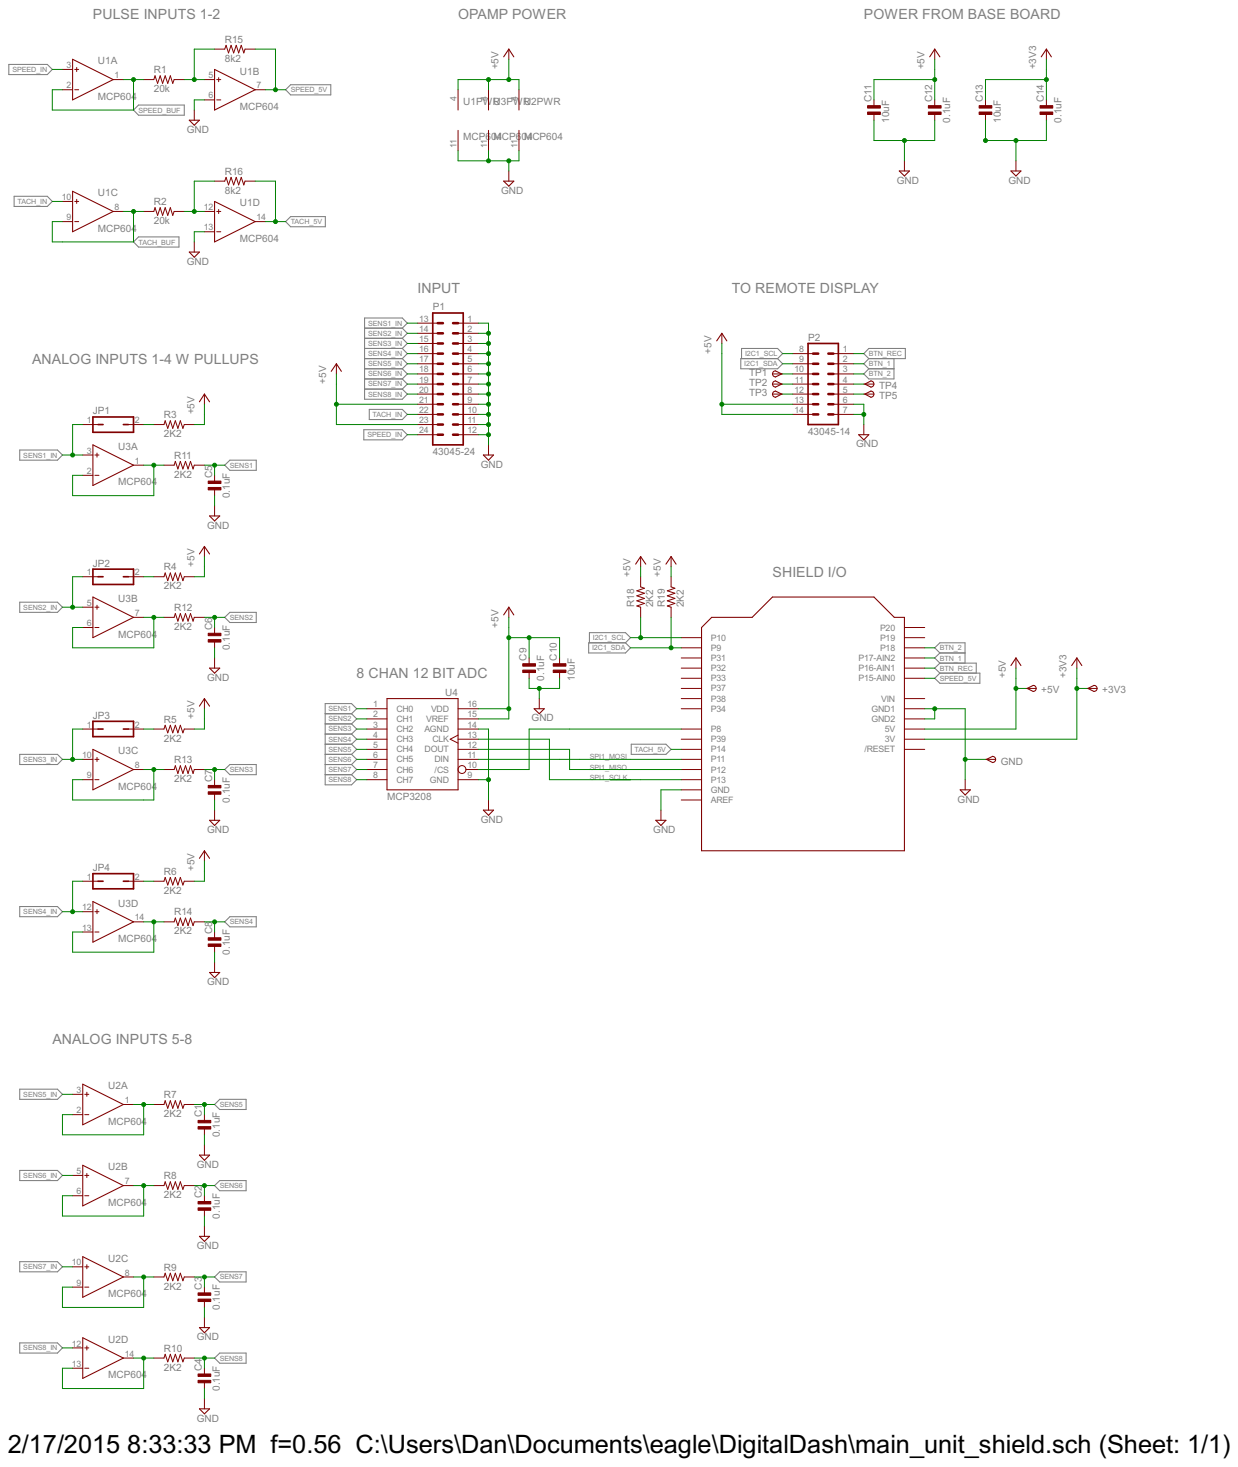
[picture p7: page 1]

2/17/2015 8:33:33 PM f=0.56 C:\Users\Dan\Documents\eagle\DigitalDash\main_unit_shield.sch (Sheet: 1/1)

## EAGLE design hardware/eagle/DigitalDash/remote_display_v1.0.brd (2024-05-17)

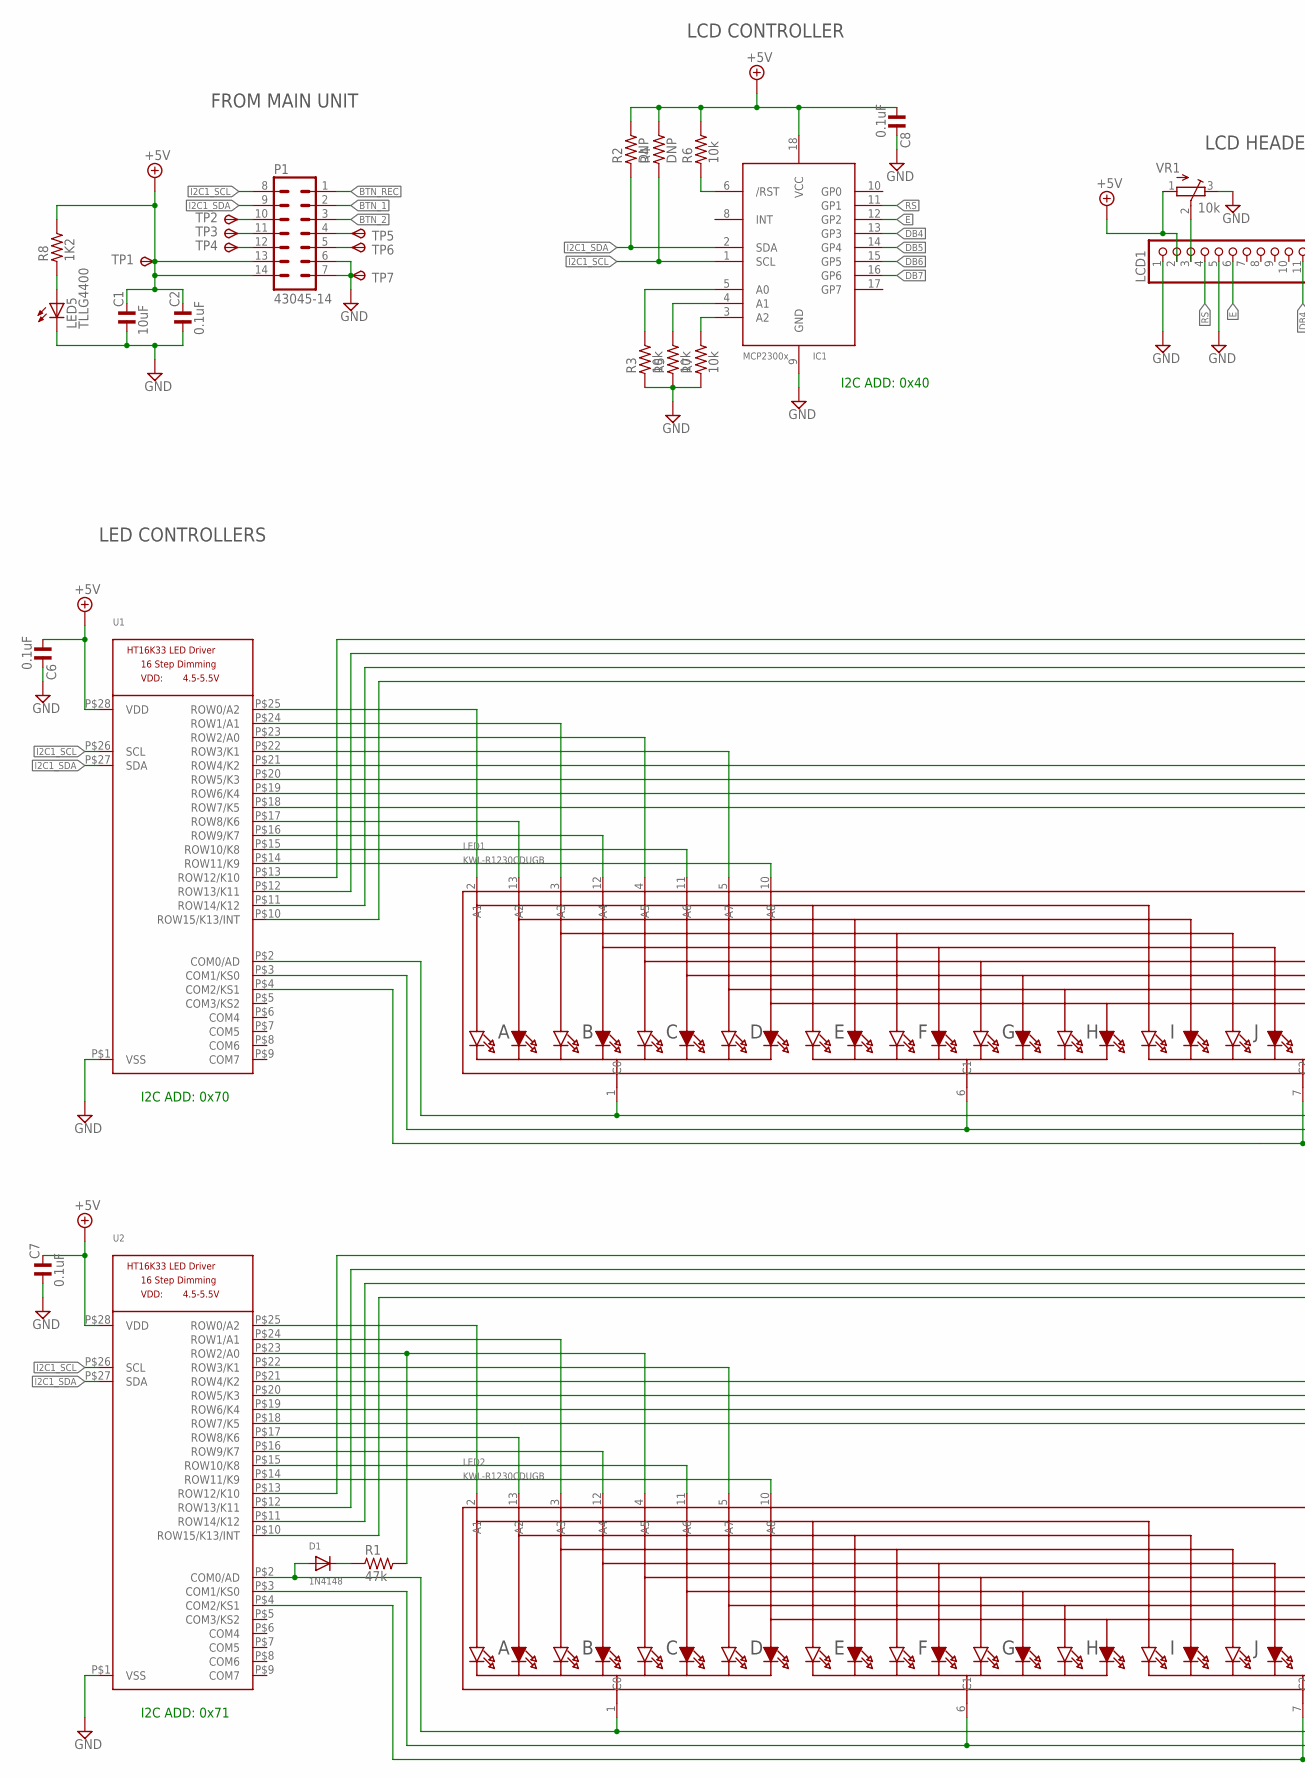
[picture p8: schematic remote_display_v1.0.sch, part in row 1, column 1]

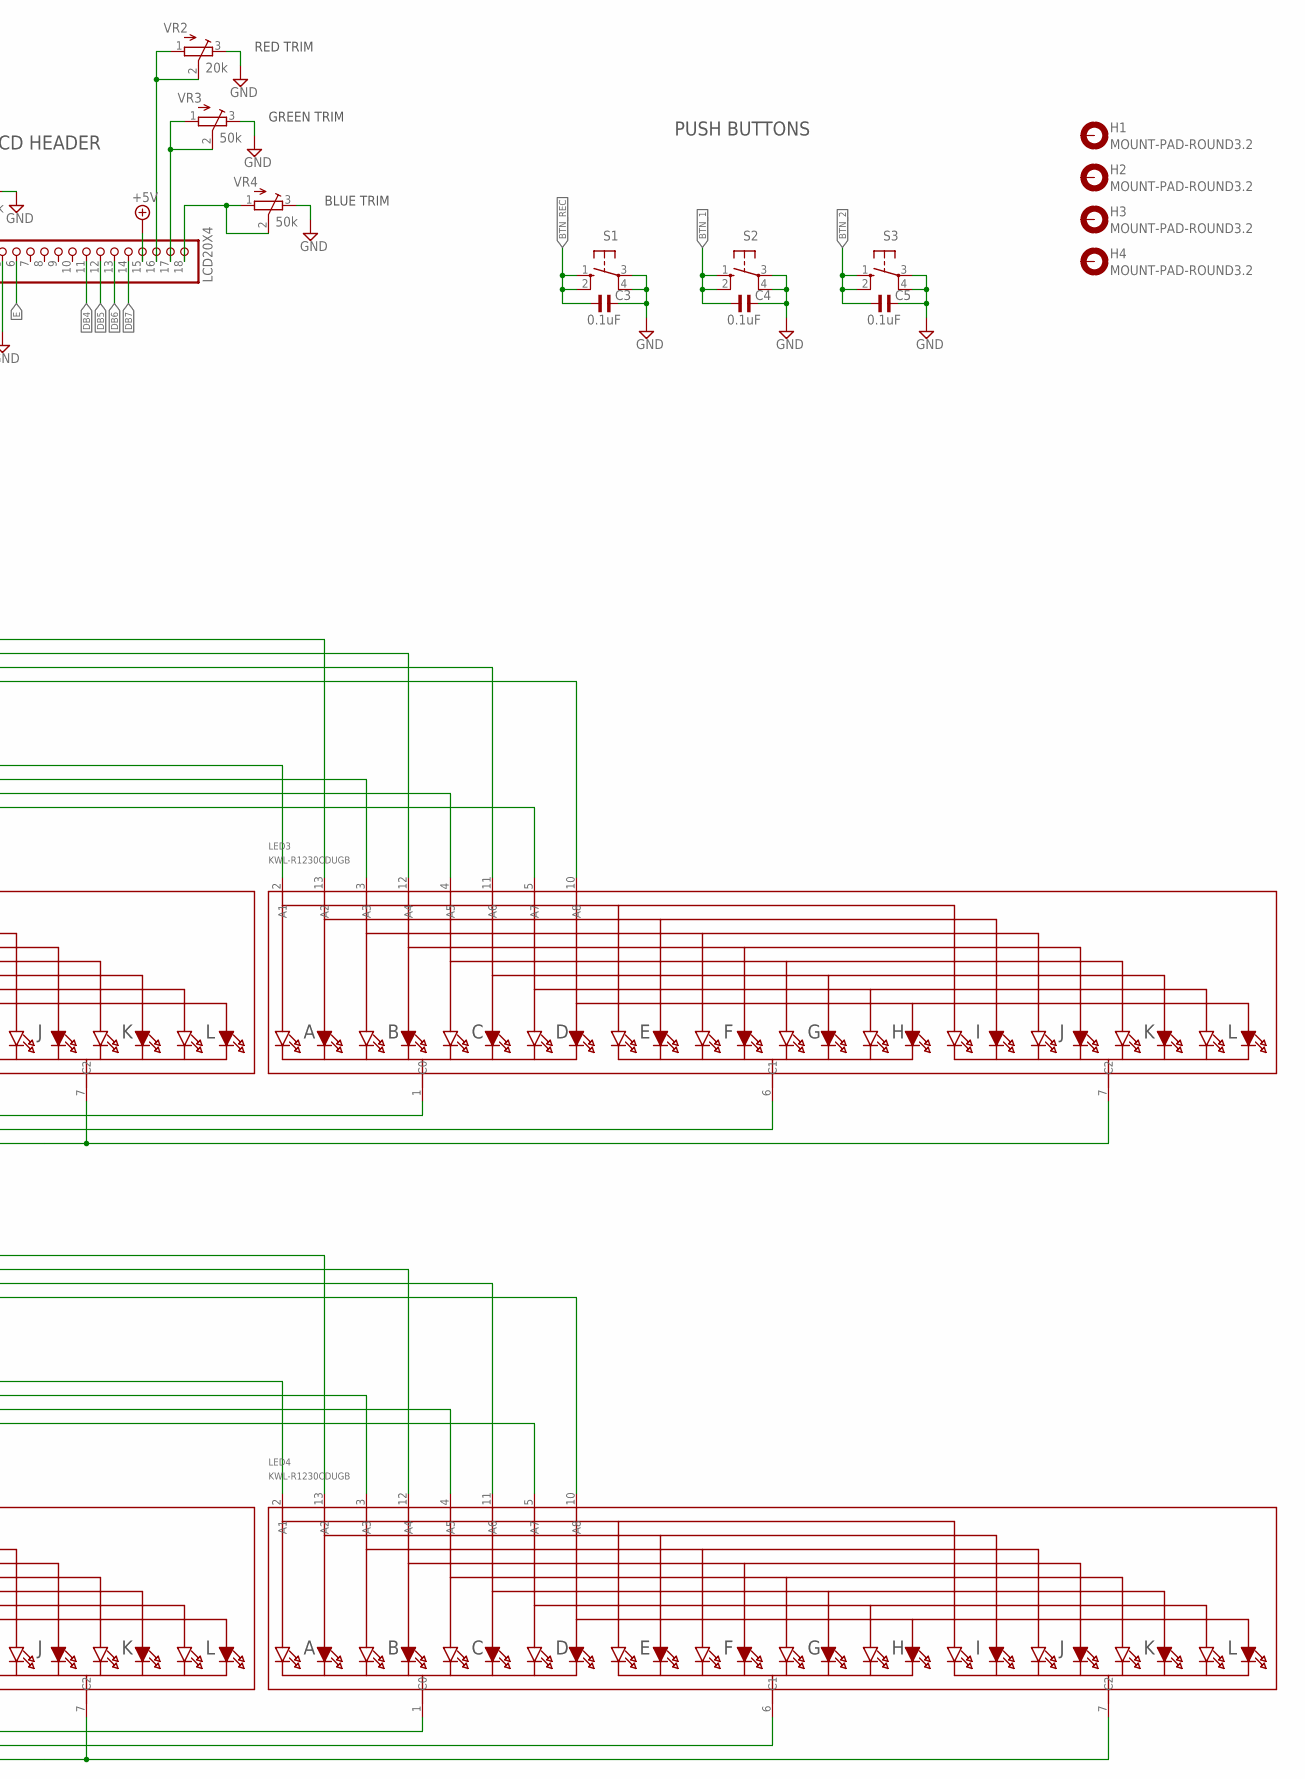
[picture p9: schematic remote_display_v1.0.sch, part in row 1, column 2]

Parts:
C1: 10uF; C0805
C2, C3, C4, C5, C6, C7, C8: 0.1uF; C0805
D1: 1N4148; SOD-323F
H1, H2, H3, H4: MOUNT-PAD-ROUND3.2; 3,2-PAD
IC1: MCP2300X/SO; SO18W
LCD1: LCD20X4
LED1, LED2, LED3, LED4: KWL-R1230CDUGB; SEGMENT_BICOL_BL-AR12Z3010
LED5: TLLG4400; LED3MM
P1: 43045-14
R1: 47k; R0805; MPN CRCW080547K0FKEAHP
R2, R4: DNP; R0805; MPN CRCW080510K0FKTA
R3, R5, R6, R7: 10k; R0805; MPN CRCW080510K0FKTA
R8: 1K2; R0805; MPN CRCW080510K0FKTA
S1, S2, S3: 10-XX; B3F-10XX
TP1, TP2, TP3, TP4, TP5, TP6, TP7: TPSPAD1-13; P1-13
U1, U2: HT16K33_SOP28; SOP28_300MIL
VR1: 10k; TC33X
VR2: 20k; TC33X
VR3, VR4: 50k; TC33X

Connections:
+5V: C1.2, C2.2, C6.1, C7.2, C8.1, IC1.18 (VCC), LCD1.2, LCD1.15, P1.13, P1.14, R2.2, R4.2, R6.2, R8.2, TP1.TP, U1.P$28 (VDD), U2.P$28 (VDD), VR1.1 (A)
BTN_1: C4.1, P1.2, S2.1 (S), S2.2 (S1)
BTN_2: C5.1, P1.3, S3.1 (S), S3.2 (S1)
BTN_REC: C3.1, P1.1, S1.1 (S), S1.2 (S1)
DB4: IC1.13 (GP3), LCD1.11
DB5: IC1.14 (GP4), LCD1.12
DB6: IC1.15 (GP5), LCD1.13
DB7: IC1.16 (GP6), LCD1.14
E: IC1.12 (GP2), LCD1.6
GND: C1.1, C2.1, C3.2, C4.2, C5.2, C6.2, C7.1, C8.2, IC1.9 (GND), LCD1.1, LCD1.5, LED5.K (C), P1.6, P1.7, R3.1, R5.1, R7.1, S1.3, S1.4 (P1), S2.3, S2.4 (P1), S3.3, S3.4 (P1), TP7.TP, U1.P$1 (VSS), U2.P$1 (VSS), VR1.3 (E), VR2.3 (E), VR3.3 (E), VR4.3 (E)
I2C1_SCL: IC1.1 (SCL), P1.8, R4.1, U1.P$26 (SCL), U2.P$26 (SCL)
I2C1_SDA: IC1.2 (SDA), P1.9, R2.1, U1.P$27 (SDA), U2.P$27 (SDA)
unnamed: LCD1.17, VR3.1 (A), VR3.2 (S)
unnamed: D1.C, R1.1
unnamed: LCD1.3, VR1.2 (S)
unnamed: IC1.3 (A2), R7.2
unnamed: IC1.4 (A1), R5.2
unnamed: LED1.2 (A1), U1.P$25 (ROW0/A2)
unnamed: LCD1.16, VR2.1 (A), VR2.2 (S)
unnamed: LED1.7 (C2), LED3.7 (C2), U1.P$4 (COM2/KS1)
unnamed: IC1.6 (/RST), R6.1
unnamed: LED5.A, R8.1
unnamed: LED1.1 (C0), LED3.1 (C0), U1.P$2 (COM0/AD)
unnamed: LED1.6 (C1), LED3.6 (C1), U1.P$3 (COM1/KS0)
unnamed: LED1.3 (A3), U1.P$24 (ROW1/A1)
unnamed: LED1.13 (A2), U1.P$17 (ROW8/K6)
unnamed: LED1.12 (A4), U1.P$16 (ROW9/K7)
unnamed: LED1.11 (A6), U1.P$15 (ROW10/K8)
unnamed: LED1.10 (A8), U1.P$14 (ROW11/K9)
unnamed: LED1.5 (A7), U1.P$22 (ROW3/K1)
unnamed: LED1.4 (A5), U1.P$23 (ROW2/A0)
unnamed: LED3.2 (A1), U1.P$21 (ROW4/K2)
unnamed: LED3.3 (A3), U1.P$20 (ROW5/K3)
unnamed: LED3.4 (A5), U1.P$19 (ROW6/K4)
unnamed: LED3.5 (A7), U1.P$18 (ROW7/K5)
unnamed: LED3.13 (A2), U1.P$13 (ROW12/K10)
unnamed: IC1.5 (A0), R3.2
unnamed: P1.5, TP6.TP
unnamed: LED3.12 (A4), U1.P$12 (ROW13/K11)
unnamed: LED3.11 (A6), U1.P$11 (ROW14/K12)
unnamed: LED3.10 (A8), U1.P$10 (ROW15/K13/INT)
unnamed: D1.A, LED2.1 (C0), LED4.1 (C0), U2.P$2 (COM0/AD)
unnamed: LED2.6 (C1), LED4.6 (C1), U2.P$3 (COM1/KS0)
unnamed: LED2.7 (C2), LED4.7 (C2), U2.P$4 (COM2/KS1)
unnamed: LED2.2 (A1), U2.P$25 (ROW0/A2)
unnamed: LED2.3 (A3), U2.P$24 (ROW1/A1)
unnamed: LED2.13 (A2), U2.P$17 (ROW8/K6)
unnamed: LED2.12 (A4), U2.P$16 (ROW9/K7)
unnamed: LED2.11 (A6), U2.P$15 (ROW10/K8)
unnamed: LCD1.18, VR4.1 (A), VR4.2 (S)
unnamed: LED2.10 (A8), U2.P$14 (ROW11/K9)
unnamed: LED2.5 (A7), U2.P$22 (ROW3/K1)
unnamed: LED2.4 (A5), R1.2, U2.P$23 (ROW2/A0)
unnamed: LED4.2 (A1), U2.P$21 (ROW4/K2)
unnamed: LED4.3 (A3), U2.P$20 (ROW5/K3)
unnamed: LED4.4 (A5), U2.P$19 (ROW6/K4)
unnamed: LED4.5 (A7), U2.P$18 (ROW7/K5)
unnamed: LED4.13 (A2), U2.P$13 (ROW12/K10)
unnamed: LED4.12 (A4), U2.P$12 (ROW13/K11)
unnamed: LED4.11 (A6), U2.P$11 (ROW14/K12)
unnamed: LED4.10 (A8), U2.P$10 (ROW15/K13/INT)
unnamed: P1.4, TP5.TP
unnamed: P1.12, TP4.TP
unnamed: P1.11, TP3.TP
unnamed: P1.10, TP2.TP
RS: IC1.11 (GP1), LCD1.4

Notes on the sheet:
I2C ADD: 0x70
I2C ADD: 0x71
I2C ADD: 0x40
FROM MAIN UNIT
LCD CONTROLLER
LCD HEADER
PUSH BUTTONS
LED CONTROLLERS
RED TRIM
GREEN TRIM
BLUE TRIM

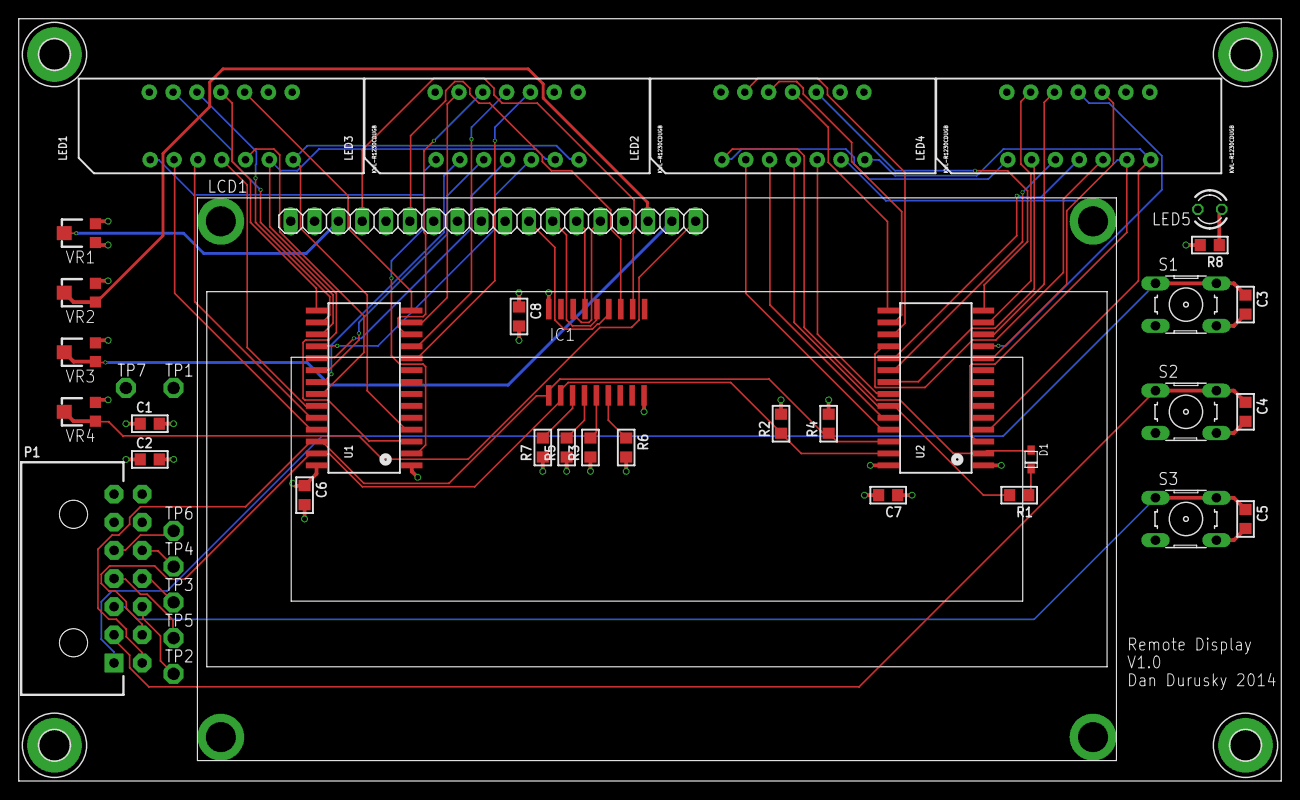
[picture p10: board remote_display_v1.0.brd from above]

Board: 4 copper layers, 134.6 x 81.3 mm, 45 parts (0 on the bottom side), 66 nets.

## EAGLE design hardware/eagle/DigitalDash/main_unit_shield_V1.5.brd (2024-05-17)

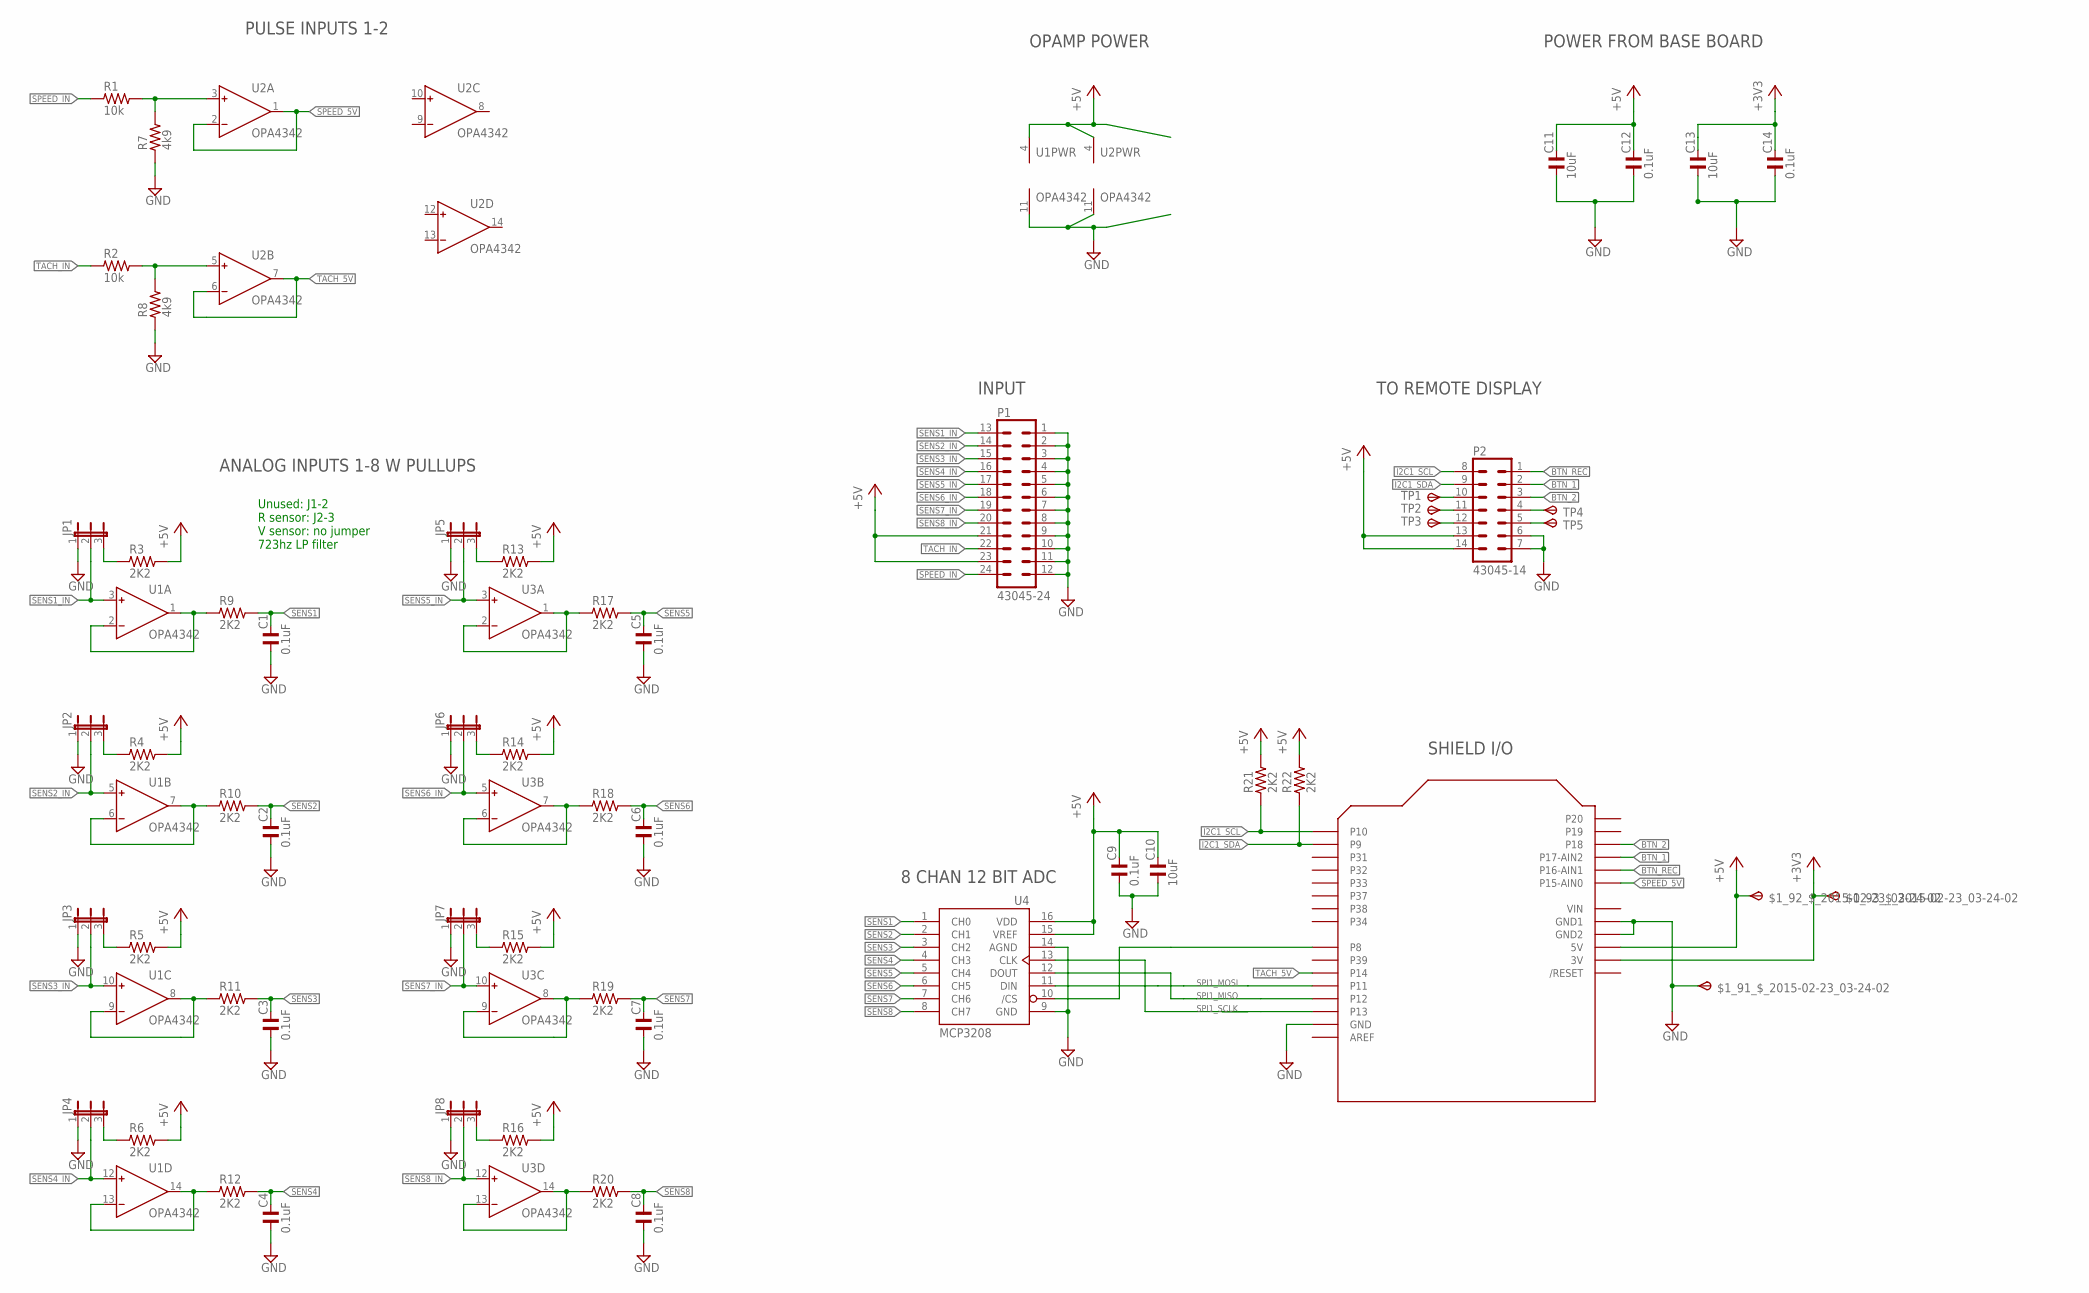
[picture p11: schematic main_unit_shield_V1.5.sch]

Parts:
$1_91_$_2015-02-23_03-24-02, $1_92_$_2015-02-23_03-24-02, $1_93_$_2015-02-23_03-24-02: TPSPAD1-13; P1-13
C1, C2, C3, C4, C5, C6, C7, C8, C9, C12, C14: 0.1uF; C0805; MPN C2012X7R1H104K085AA
C10, C11, C13: 10uF; C0805; MPN C2012X5R1E106K125AB
JP1, JP2, JP3, JP4, JP5, JP6, JP7, JP8: JP2E; JP2
P1: 43045-24; MPN 43045-2400
P2: 43045-14; MPN 43045-1400
R1: 10k; R0805; MPN CRCW08058K20FKEAHP
R2: 10k; R0805; MPN CRCW080520K0FKEA
R3, R4, R5, R6, R9, R10, R11, R12, R13, R14, R15, R16, R17, R18, R19, R20, R21, R22: 2K2; R0805; MPN CRCW08052K20FKEA
R7: 4k9; R0805; MPN CRCW080520K0FKEA
R8: 4k9; R0805; MPN CRCW08058K20FKEAHP
TP1, TP2, TP3, TP4, TP5: TPSPAD1-13; P1-13
U1, U2, U3: OPA4342; SO14
U4: MCP3208; SO16; MPN MCP3208-BI/SL
U6: ARDUINOUNO; ARDUINO

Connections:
+3V3: $1_93_$_2015-02-23_03-24-02.TP, C13.2, C14.2, U6.3V
+5V: $1_92_$_2015-02-23_03-24-02.TP, C9.2, C10.2, C11.2, C12.2, P1.21, P1.23, P2.13, P2.14, R3.2, R4.2, R5.2, R6.2, R13.2, R14.2, R15.2, R16.2, R21.2, R22.2, U1.4 (V+), U2.4 (V+), U4.15 (VREF), U4.16 (VDD), U6.5V
BTN_1: P2.2, U6.A2 (P17-AIN2)
BTN_2: P2.3, U6.A3 (P18)
BTN_REC: P2.1, U6.A1 (P16-AIN1)
GND: $1_91_$_2015-02-23_03-24-02.TP, C1.1, C2.1, C3.1, C4.1, C5.1, C6.1, C7.1, C8.1, C9.1, C10.1, C11.1, C12.1, C13.1, C14.1, JP1.1, JP2.1, JP3.1, JP4.1, JP5.1, JP6.1, JP7.1, JP8.1, P1.1, P1.2, P1.3, P1.4, P1.5, P1.6, P1.7, P1.8, P1.9, P1.10, P1.11, P1.12, P2.6, P2.7, R7.1, R8.1, U1.11 (V-), U2.11 (V-), U4.9 (GND), U4.14 (AGND), U6.GND, U6.GND1, U6.GND2
I2C1_SCL: P2.8, R21.1, U6.D0 (P10)
I2C1_SDA: P2.9, R22.1, U6.D1 (P9)
unnamed: R1.2, R7.2, U2.3 (IN+)
unnamed: JP1.3, R3.1
unnamed: R2.2, R8.2, U2.5 (IN+)
unnamed: JP2.3, R4.1
unnamed: JP3.3, R5.1
unnamed: U4.10 (/CS), U6.D8 (P8)
unnamed: JP5.3, R13.1
unnamed: JP4.3, R6.1
unnamed: JP6.3, R14.1
unnamed: JP7.3, R15.1
unnamed: JP8.3, R16.1
unnamed: R9.1, U1.1 (OUT), U1.2 (IN-)
unnamed: P2.10, TP1.TP
unnamed: P2.11, TP2.TP
unnamed: P2.12, TP3.TP
unnamed: P2.4, TP4.TP
unnamed: P2.5, TP5.TP
SENS1: C1.2, R9.2, U4.1 (CH0)
SENS1_BUF1: R17.1, U3.1 (OUT), U3.2 (IN-)
SENS1_IN: JP1.2, P1.13, U1.3 (IN+)
SENS2: C2.2, R10.2, U4.2 (CH1)
SENS2_BUF: R10.1, U1.6 (IN-), U1.7 (OUT)
SENS2_BUF1: R18.1, U3.6 (IN-), U3.7 (OUT)
SENS2_IN: JP2.2, P1.14, U1.5 (IN+)
SENS3: C3.2, R11.2, U4.3 (CH2)
SENS3_BUF: R11.1, U1.8 (OUT), U1.9 (IN-)
SENS3_BUF1: R19.1, U3.8 (OUT), U3.9 (IN-)
SENS3_IN: JP3.2, P1.15, U1.10 (IN+)
SENS4: C4.2, R12.2, U4.4 (CH3)
SENS4_BUF: R12.1, U1.13 (IN-), U1.14 (OUT)
SENS4_BUF1: R20.1, U3.13 (IN-), U3.14 (OUT)
SENS4_IN: JP4.2, P1.16, U1.12 (IN+)
SENS5: C5.2, R17.2, U4.5 (CH4)
SENS5_IN: JP5.2, P1.17, U3.3 (IN+)
SENS6: C6.2, R18.2, U4.6 (CH5)
SENS6_IN: JP6.2, P1.18, U3.5 (IN+)
SENS7: C7.2, R19.2, U4.7 (CH6)
SENS7_IN: JP7.2, P1.19, U3.10 (IN+)
SENS8: C8.2, R20.2, U4.8 (CH7)
SENS8_IN: JP8.2, P1.20, U3.12 (IN+)
SPEED_5V: U2.1 (OUT), U2.2 (IN-), U6.A0 (P15-AIN0)
SPEED_IN: P1.24, R1.1
SPI1_MISO: U4.12 (DOUT), U6.D12 (P12)
SPI1_MOSI: U4.11 (DIN), U6.D11 (P11)
SPI1_SCLK: U4.13 (CLK), U6.D13 (P13)
TACH_5V: U2.6 (IN-), U2.7 (OUT), U6.D10 (P14)
TACH_IN: P1.22, R2.1
V+: U3.4 (V+)
V-: U3.11 (V-)
VIN: U6.VIN

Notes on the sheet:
ANALOG INPUTS 1-8 W PULLUPS
PULSE INPUTS 1-2
TO REMOTE DISPLAY
SHIELD I/O
8 CHAN 12 BIT ADC
OPAMP POWER
POWER FROM BASE BOARD
INPUT
Unused: J1-2 R sensor: J2-3 V sensor: no jumper 723hz LP filter

Board: 4 copper layers, 59 parts (0 on the bottom side), 55 nets, no tracks yet.

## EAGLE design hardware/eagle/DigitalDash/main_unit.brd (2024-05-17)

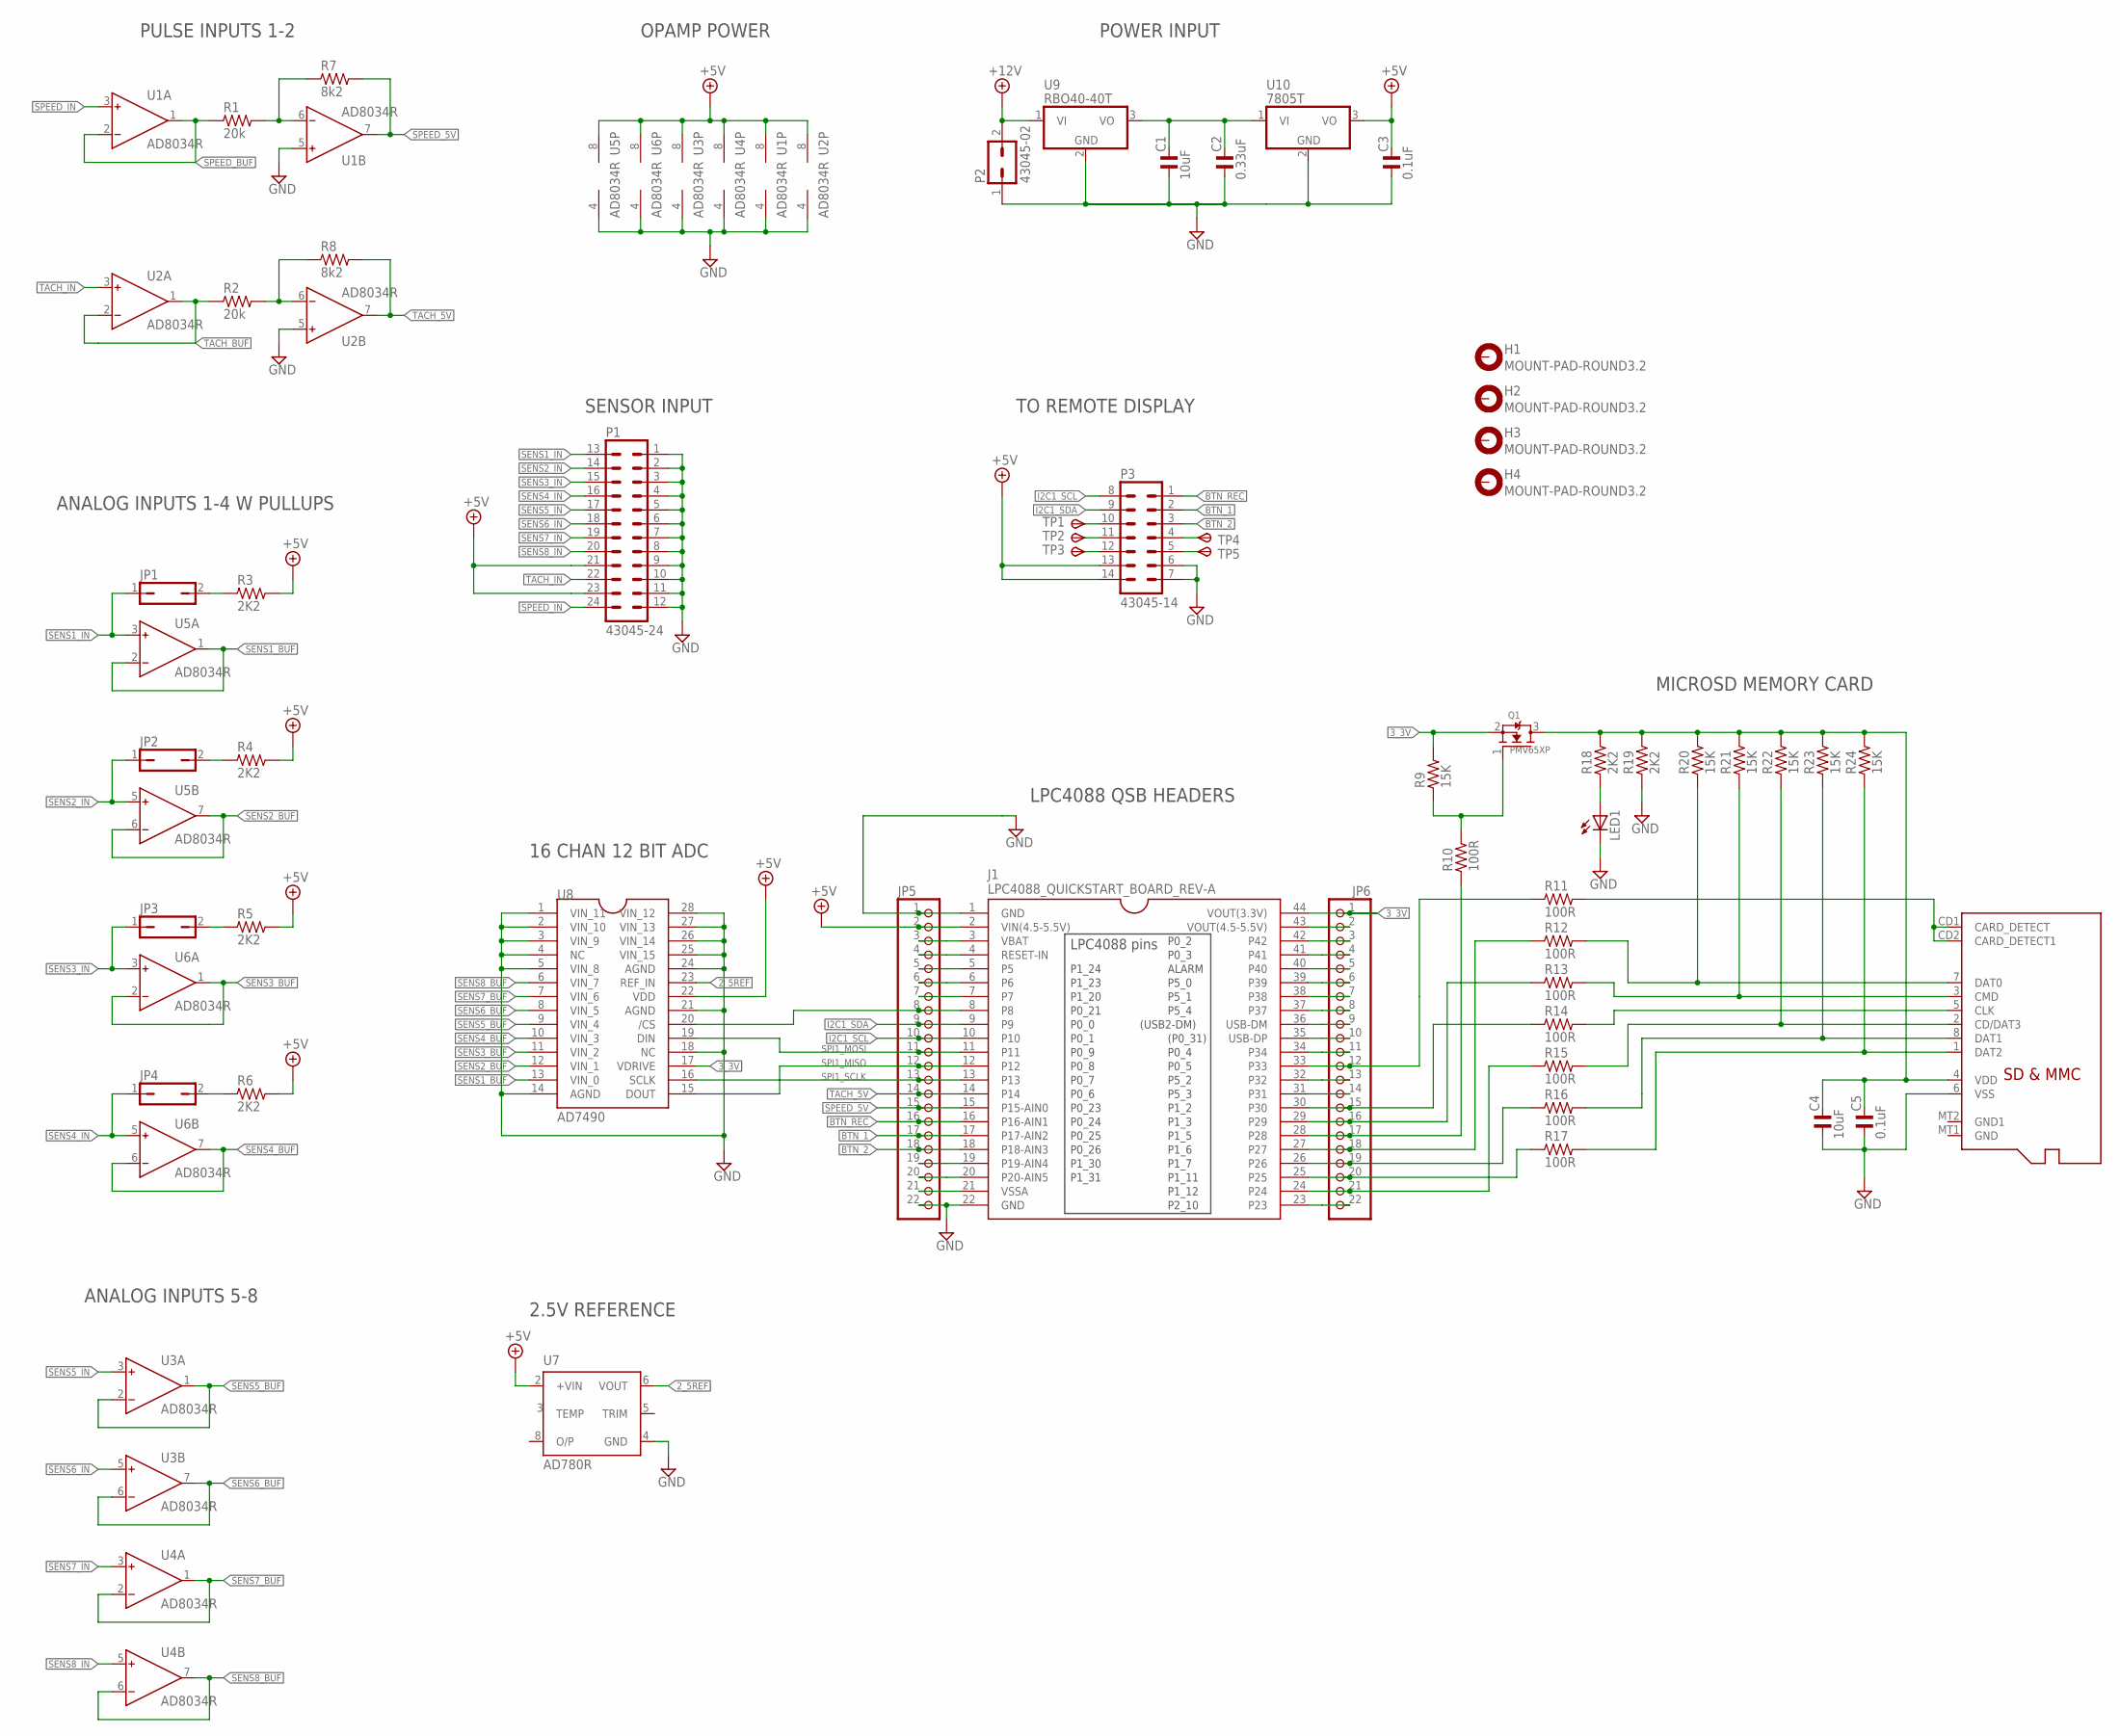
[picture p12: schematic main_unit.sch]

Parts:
C1, C4: 10uF; C0805
C2: 0.33uF; C0805
C3, C5: 0.1uF; C0805
H1, H2, H3, H4: MOUNT-PAD-ROUND3.2; 3,2-PAD
J1: LPC4088_QUICKSTART_BOARD_REV-A
JP1, JP2, JP3, JP4: JP1Q; JP1
JP5, JP6: PINHD-1X22; 1X22
LED1: LEDCHIP-LED0805; CHIP-LED0805
P1: 43045-24
P2: 43045-02
P3: 43045-14
Q1: PMV65XP; SOT23
R1, R2: 20k; R0805
R3, R4, R5, R6, R18, R19: 2K2; R0805
R7, R8: 8k2; R0805
R9, R20, R21, R22, R23, R24: 15K; R0805
R10, R11, R12, R13, R14, R15, R16, R17: 100R; R0805
SD1: MICROSD_SDMODE; MICROSD
TP1, TP2, TP3, TP4, TP5: TPSPAD1-13; P1-13
U1, U2, U3, U4, U5, U6: AD8034R; SO8
U7: AD780R; SO8
U8: AD7490; TSSOP28
U9: RBO40-40T; TO220H
U10: 7805T; TO220H

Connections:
2_5REF: U7.6 (VOUT), U8.23 (REF_IN)
3_3V: J1.44 (VOUT(3.3V)), JP6.1, Q1.2 (S), R9.2, U8.17 (VDRIVE)
+5V: C3.2, J1.2 (VIN(4.5-5.5V)), JP5.2, P1.21, P1.23, P3.13, P3.14, R3.2, R4.2, R5.2, R6.2, U1.8 (V+), U2.8 (V+), U3.8 (V+), U4.8 (V+), U5.8 (V+), U6.8 (V+), U7.2 (+VIN), U8.22 (VDD), U10.3 (VO)
+12V: P2.2, U9.1 (VI)
BTN_1: J1.17 (P17-AIN2), JP5.17, P3.2
BTN_2: J1.18 (P18-AIN3), JP5.18, P3.3
BTN_REC: J1.16 (P16-AIN1), JP5.16, P3.1
GND: C1.1, C2.1, C3.1, C4.1, C5.1, J1.1 (GND), J1.22 (GND), JP5.1, JP5.22, LED1.C, P1.1, P1.2, P1.3, P1.4, P1.5, P1.6, P1.7, P1.8, P1.9, P1.10, P1.11, P1.12, P2.1, P3.6, P3.7, R19.1, SD1.6 (VSS), U1.4 (V-), U1.5 (IN+), U2.4 (V-), U2.5 (IN+), U3.4 (V-), U4.4 (V-), U5.4 (V-), U6.4 (V-), U7.4 (GND), U8.1 (VIN_11), U8.2 (VIN_10), U8.3 (VIN_9), U8.4 (NC), U8.5 (VIN_8), U8.14 (AGND), U8.18 (NC), U8.21 (AGND), U8.24 (AGND), U8.25 (VIN_15), U8.26 (VIN_14), U8.27 (VIN_13), U8.28 (VIN_12), U9.2 (GND), U10.2 (GND)
I2C1_SCL: J1.10, JP5.10, P3.8
I2C1_SDA: J1.9, JP5.9, P3.9
unnamed: R1.2, R7.1, U1.6 (IN-)
unnamed: R12.2, R20.1, SD1.7 (DAT0)
unnamed: R2.2, R8.1, U2.6 (IN-)
unnamed: R13.2, R21.1, SD1.3 (CMD)
unnamed: R14.2, SD1.5 (CLK)
unnamed: J1.8, JP5.8, U8.20 (/CS)
unnamed: R15.2, R22.1, SD1.2 (CD/DAT3)
unnamed: R16.2, R23.1, SD1.8 (DAT1)
unnamed: R17.2, R24.1, SD1.1 (DAT2)
unnamed: JP1.2, R3.1
unnamed: J1.27, JP6.18, R12.1
unnamed: J1.29, JP6.16, R13.1
unnamed: J1.30, JP6.15, R14.1
unnamed: J1.26, JP6.19, R16.1
unnamed: J1.25, JP6.20, R17.1
unnamed: J1.24, JP6.21, R15.1
unnamed: J1.28, JP6.17, R10.1
unnamed: Q1.1 (G), R9.1, R10.2
unnamed: LED1.A, R18.1
unnamed: R11.2, SD1.CD1 (CARD_DETECT), SD1.CD2 (CARD_DETECT1)
unnamed: JP3.2, R5.1
unnamed: J1.38, JP6.7
unnamed: P3.10, TP1.TP
unnamed: P3.11, TP2.TP
unnamed: JP2.2, R4.1
unnamed: C1.2, C2.2, U9.3 (VO), U10.1 (VI)
unnamed: P3.12, TP3.TP
unnamed: J1.3 (VBAT), JP5.3
unnamed: JP4.2, R6.1
unnamed: J1.4 (RESET-IN), JP5.4
unnamed: P3.4, TP4.TP
unnamed: J1.5, JP5.5
unnamed: J1.6, JP5.6
unnamed: P3.5, TP5.TP
unnamed: J1.7, JP5.7
unnamed: J1.19 (P19-AIN4), JP5.19
unnamed: J1.20 (P20-AIN5), JP5.20
unnamed: J1.21 (VSSA), JP5.21
unnamed: J1.43 (VOUT(4.5-5.5V)), JP6.2
unnamed: J1.42, JP6.3
unnamed: J1.41, JP6.4
unnamed: J1.40, JP6.5
unnamed: J1.39, JP6.6
unnamed: J1.37, JP6.8
unnamed: J1.36 (USB-DM), JP6.9
unnamed: J1.35 (USB-DP), JP6.10
unnamed: J1.34, JP6.11
unnamed: J1.33, JP6.12, R11.1
unnamed: J1.32, JP6.13
unnamed: J1.31, JP6.14
unnamed: J1.23, JP6.22
SENS1_BUF: U5.1 (OUT), U5.2 (IN-), U8.13 (VIN_0)
SENS1_IN: JP1.1, P1.13, U5.3 (IN+)
SENS2_BUF: U5.6 (IN-), U5.7 (OUT), U8.12 (VIN_1)
SENS2_IN: JP2.1, P1.14, U5.5 (IN+)
SENS3_BUF: U6.1 (OUT), U6.2 (IN-), U8.11 (VIN_2)
SENS3_IN: JP3.1, P1.15, U6.3 (IN+)
SENS4_BUF: U6.6 (IN-), U6.7 (OUT), U8.10 (VIN_3)
SENS4_IN: JP4.1, P1.16, U6.5 (IN+)
SENS5_BUF: U3.1 (OUT), U3.2 (IN-), U8.9 (VIN_4)
SENS5_IN: P1.17, U3.3 (IN+)
SENS6_BUF: U3.6 (IN-), U3.7 (OUT), U8.8 (VIN_5)
SENS6_IN: P1.18, U3.5 (IN+)
SENS7_BUF: U4.1 (OUT), U4.2 (IN-), U8.7 (VIN_6)
SENS7_IN: P1.19, U4.3 (IN+)
SENS8_BUF: U4.6 (IN-), U4.7 (OUT), U8.6 (VIN_7)
SENS8_IN: P1.20, U4.5 (IN+)
SPEED_5V: J1.15 (P15-AIN0), JP5.15, R7.2, U1.7 (OUT)
SPEED_BUF: R1.1, U1.1 (OUT), U1.2 (IN-)
SPEED_IN: P1.24, U1.3 (IN+)
SPI1_MISO: J1.12, JP5.12, U8.15 (DOUT)
SPI1_MOSI: J1.11, JP5.11, U8.19 (DIN)
SPI1_SCLK: J1.13, JP5.13, U8.16 (SCLK)
TACH_5V: J1.14, JP5.14, R8.2, U2.7 (OUT)
TACH_BUF: R2.1, U2.1 (OUT), U2.2 (IN-)
TACH_IN: P1.22, U2.3 (IN+)
VDD: C4.2, C5.2, Q1.3 (D), R18.2, R19.2, R20.2, R21.2, R22.2, R23.2, R24.2, SD1.4 (VDD)

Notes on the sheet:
ANALOG INPUTS 1-4 W PULLUPS
PULSE INPUTS 1-2
TO REMOTE DISPLAY
LPC4088 QSB HEADERS
MICROSD MEMORY CARD
16 CHAN 12 BIT ADC
2.5V REFERENCE
OPAMP POWER
POWER INPUT
ANALOG INPUTS 5-8
SENSOR INPUT

Board: 4 copper layers, 61 parts (0 on the bottom side), 87 nets, no tracks yet.

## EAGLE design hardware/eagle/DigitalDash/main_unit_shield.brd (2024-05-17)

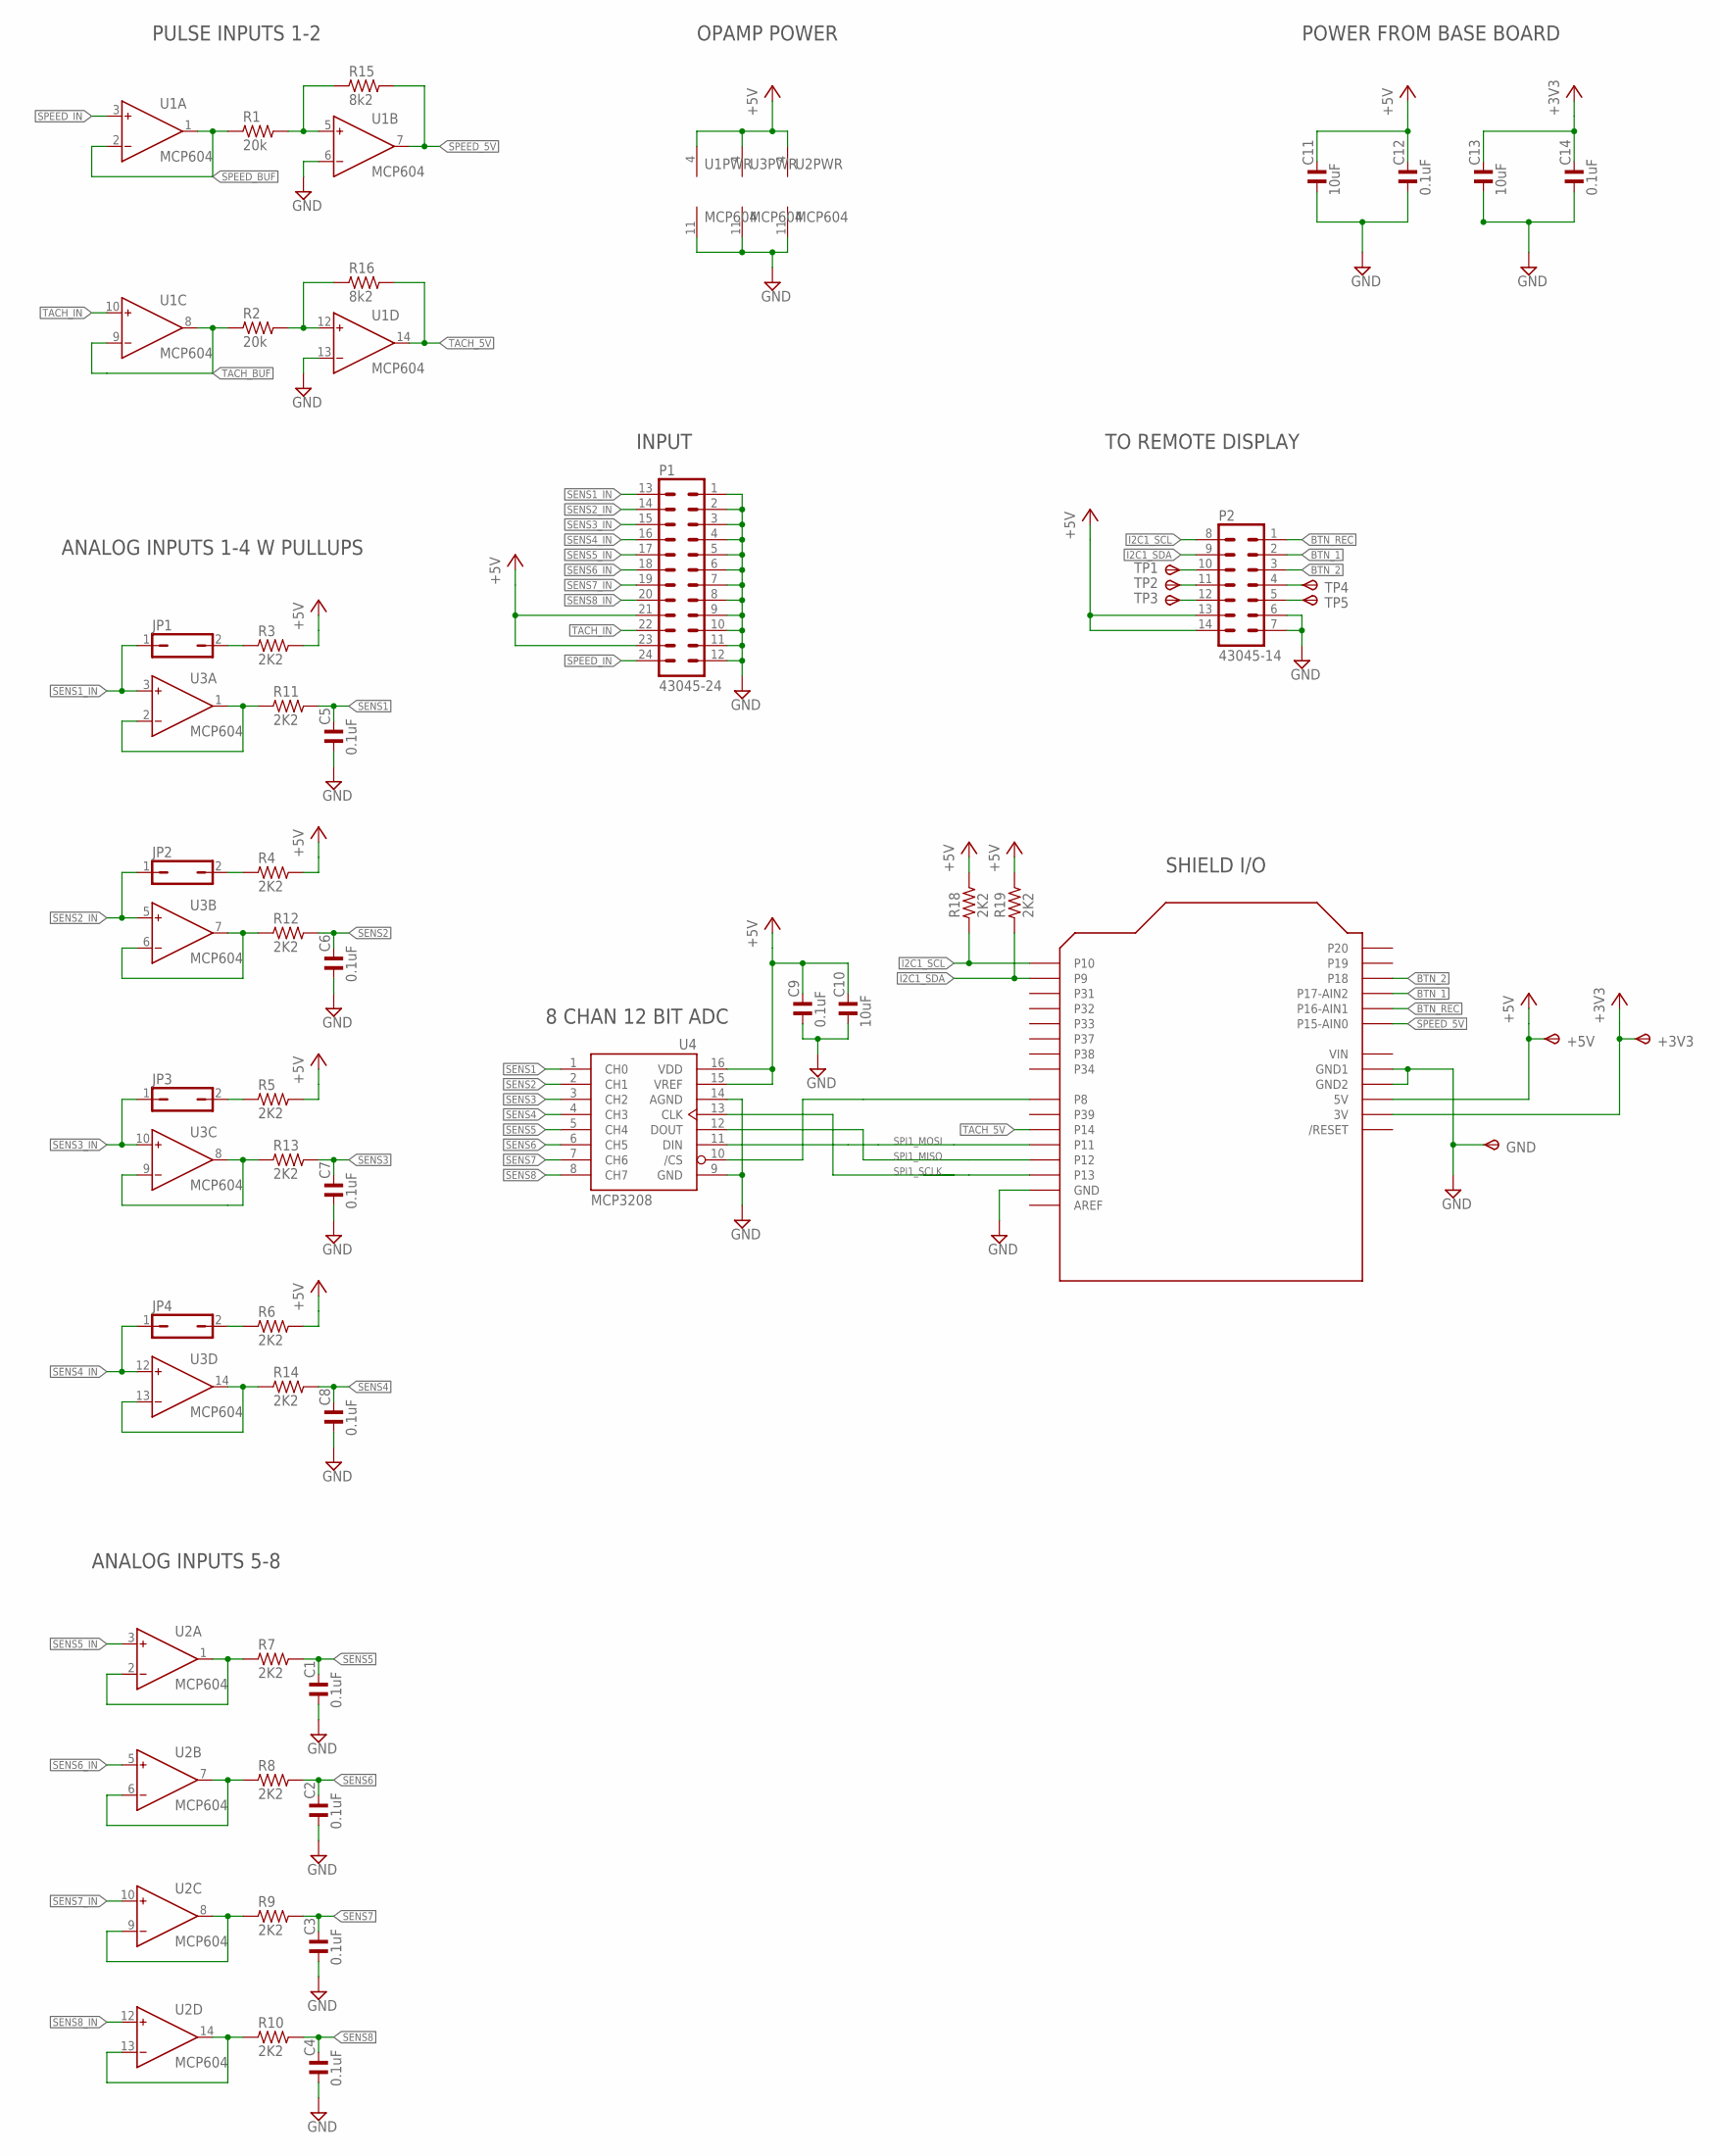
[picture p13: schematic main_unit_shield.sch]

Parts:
+3V3, +5V: TPSPAD1-13; P1-13
C1, C2, C3, C4, C5, C6, C7, C8, C9, C12, C14: 0.1uF; C0805; MPN C2012X7R1H104K085AA
C10, C11, C13: 10uF; C0805; MPN C2012X5R1E106K125AB
GND: TPSPAD1-13; P1-13
JP1, JP2, JP3, JP4: JP1Q; JP1; MPN 969102-0000-DA
P1: 43045-24; MPN 43045-2400
P2: 43045-14; MPN 43045-1400
R1, R2: 20k; R0805; MPN CRCW080520K0FKEA
R3, R4, R5, R6, R7, R8, R9, R10, R11, R12, R13, R14, R18, R19: 2K2; R0805; MPN CRCW08052K20FKEA
R15, R16: 8k2; R0805; MPN CRCW08058K20FKEAHP
TP1, TP2, TP3, TP4, TP5: TPSPAD1-13; P1-13
U1, U2, U3: MCP604; SO14; MPN MCP6044-E/SL
U4: MCP3208; SO16; MPN MCP3208-BI/SL
U5: ARDUINOUNO; ARDUINO

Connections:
+3V3: +3V3.TP, C13.2, C14.2, U5.3V
+5V: +5V.TP, C9.2, C10.2, C11.2, C12.2, P1.21, P1.23, P2.13, P2.14, R3.2, R4.2, R5.2, R6.2, R18.2, R19.2, U1.4 (V+), U2.4 (V+), U3.4 (V+), U4.15 (VREF), U4.16 (VDD), U5.5V
BTN_1: P2.2, U5.A2 (P17-AIN2)
BTN_2: P2.3, U5.A3 (P18)
BTN_REC: P2.1, U5.A1 (P16-AIN1)
GND: C1.1, C2.1, C3.1, C4.1, C5.1, C6.1, C7.1, C8.1, C9.1, C10.1, C11.1, C12.1, C13.1, C14.1, GND.TP, P1.1, P1.2, P1.3, P1.4, P1.5, P1.6, P1.7, P1.8, P1.9, P1.10, P1.11, P1.12, P2.6, P2.7, U1.6 (IN-), U1.11 (V-), U1.13 (IN-), U2.11 (V-), U3.11 (V-), U4.9 (GND), U4.14 (AGND), U5.GND, U5.GND1, U5.GND2
I2C1_SCL: P2.8, R18.1, U5.D0 (P10)
I2C1_SDA: P2.9, R19.1, U5.D1 (P9)
unnamed: R1.2, R15.1, U1.5 (IN+)
unnamed: R2.2, R16.1, U1.12 (IN+)
unnamed: U4.10 (/CS), U5.D8 (P8)
unnamed: JP1.2, R3.1
unnamed: JP3.2, R5.1
unnamed: P2.10, TP1.TP
unnamed: P2.11, TP2.TP
unnamed: JP2.2, R4.1
unnamed: P2.12, TP3.TP
unnamed: JP4.2, R6.1
unnamed: P2.4, TP4.TP
unnamed: P2.5, TP5.TP
SENS1: C5.2, R11.2, U4.1 (CH0)
SENS1_BUF: R11.1, U3.1 (OUT), U3.2 (IN-)
SENS1_IN: JP1.1, P1.13, U3.3 (IN+)
SENS2: C6.2, R12.2, U4.2 (CH1)
SENS2_BUF: R12.1, U3.6 (IN-), U3.7 (OUT)
SENS2_IN: JP2.1, P1.14, U3.5 (IN+)
SENS3: C7.2, R13.2, U4.3 (CH2)
SENS3_BUF: R13.1, U3.8 (OUT), U3.9 (IN-)
SENS3_IN: JP3.1, P1.15, U3.10 (IN+)
SENS4: C8.2, R14.2, U4.4 (CH3)
SENS4_BUF: R14.1, U3.13 (IN-), U3.14 (OUT)
SENS4_IN: JP4.1, P1.16, U3.12 (IN+)
SENS5: C1.2, R7.2, U4.5 (CH4)
SENS5_BUF: R7.1, U2.1 (OUT), U2.2 (IN-)
SENS5_IN: P1.17, U2.3 (IN+)
SENS6: C2.2, R8.2, U4.6 (CH5)
SENS6_BUF: R8.1, U2.6 (IN-), U2.7 (OUT)
SENS6_IN: P1.18, U2.5 (IN+)
SENS7: C3.2, R9.2, U4.7 (CH6)
SENS7_BUF: R9.1, U2.8 (OUT), U2.9 (IN-)
SENS7_IN: P1.19, U2.10 (IN+)
SENS8: C4.2, R10.2, U4.8 (CH7)
SENS8_BUF: R10.1, U2.13 (IN-), U2.14 (OUT)
SENS8_IN: P1.20, U2.12 (IN+)
SPEED_5V: R15.2, U1.7 (OUT), U5.A0 (P15-AIN0)
SPEED_BUF: R1.1, U1.1 (OUT), U1.2 (IN-)
SPEED_IN: P1.24, U1.3 (IN+)
SPI1_MISO: U4.12 (DOUT), U5.D12 (P12)
SPI1_MOSI: U4.11 (DIN), U5.D11 (P11)
SPI1_SCLK: U4.13 (CLK), U5.D13 (P13)
TACH_5V: R16.2, U1.14 (OUT), U5.D10 (P14)
TACH_BUF: R2.1, U1.8 (OUT), U1.9 (IN-)
TACH_IN: P1.22, U1.10 (IN+)
VIN: U5.VIN

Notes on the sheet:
ANALOG INPUTS 1-4 W PULLUPS
PULSE INPUTS 1-2
TO REMOTE DISPLAY
SHIELD I/O
8 CHAN 12 BIT ADC
OPAMP POWER
POWER FROM BASE BOARD
ANALOG INPUTS 5-8
INPUT

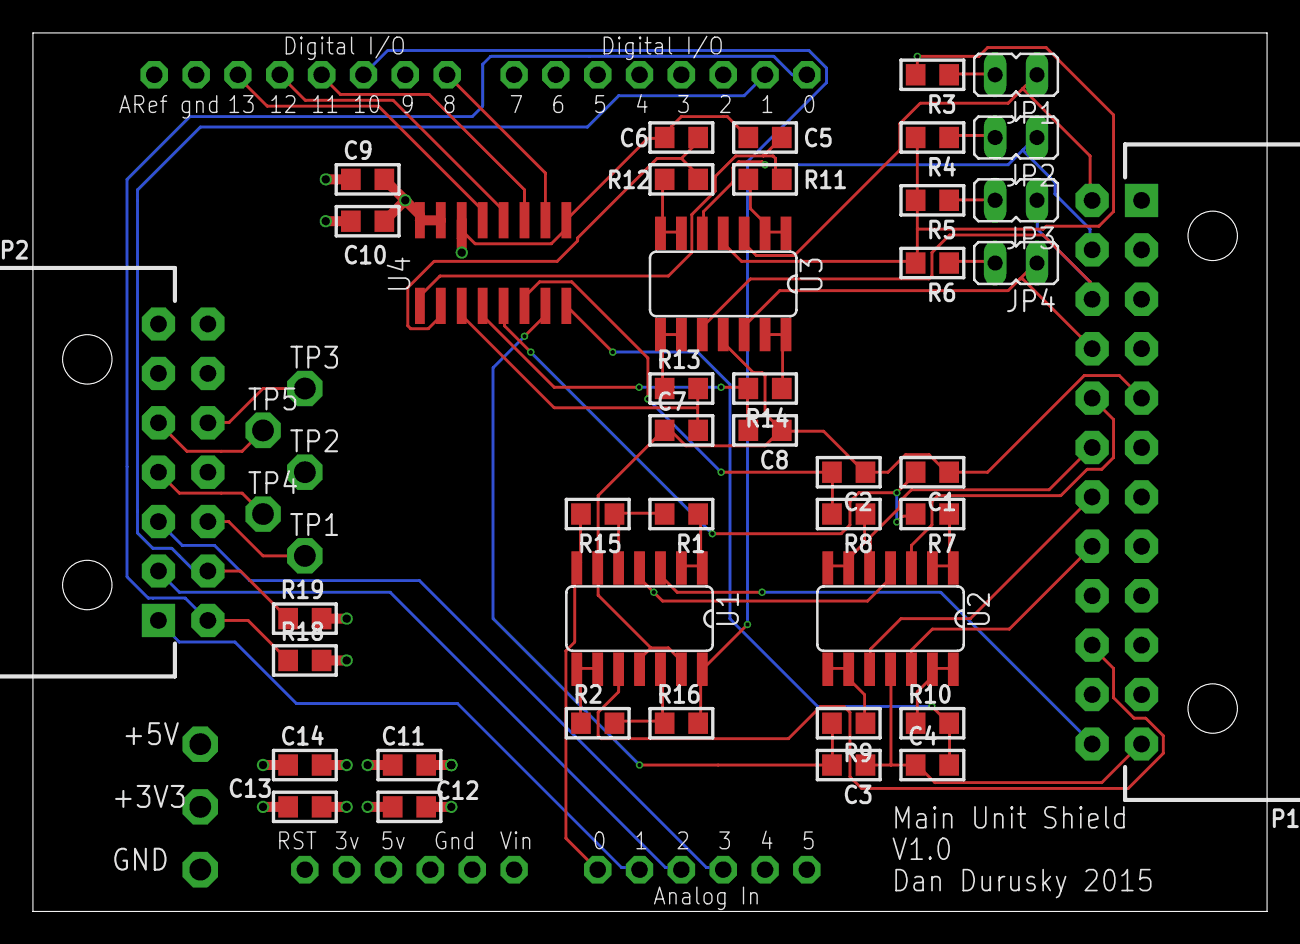
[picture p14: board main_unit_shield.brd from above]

Board: 4 copper layers, 74.9 x 53.3 mm, 51 parts (0 on the bottom side), 53 nets.

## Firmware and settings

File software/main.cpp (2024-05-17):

#include "mbed.h"
#include "MCIFileSystem.h"
#include "Adafruit_LEDBackpack.h"
#include "TextLCD.h"
#include "nmea.h" 
#include "MMA7455.h" //accelerometer
#include "mcp3208.h" // ADC
#include "structdefs.h"
#include "init.h"
#include "displayfunc.h"
 
DigitalOut led1(LED1); //active low   sampling/writing
DigitalOut led2(LED2); //active low   data logging
DigitalOut led3(LED3); //active high  RPM interrupt
DigitalOut led4(LED4); //active high  Speed interrupt
DigitalOut cs(p8);     // for SPI1

DigitalIn btn_rec(p16, PullUp);
DigitalIn btn_1(p17, PullUp);
DigitalIn btn_2(p18, PullUp);

InterruptIn rpmIntInput(p14);   // RPM pulse train
InterruptIn speedIntInput(p15); // vehicle speed pulse train

Timer rpmPulseTimer;        // counts time between pulses
Timer speedPulseTimer;      // counts time between pulses
Timer logtimer;             // for log Time
Timer logtimeouttimer;      // timer to timeout to disable logging

Ticker tenHzTicker;         //for 10hz sample rate
Ticker twohundredHzTicker;  //for button checking

NMEA nmea;                  // GPS parser
Serial pc(USBTX, USBRX);    // serial port over programming USB connection 
Serial gps(P4_22, P4_23);   // GPS receiver in Xbee socket
MCIFileSystem mcifs("mci"); // create SD card file system
SPI spi1(p11,p12,p13);      // SPI1, mosi, miso, sclk for ADC
//SPI spi2(p39,p38,p32);    // Unused
I2C i2c(p9, p10);           // SDA, SCL for shift light

MMA7455 accel(p9,p10);      // MMA7455 accelerometer
MCP3208 adc(spi1, p8);      // ADC, spi, CS
Adafruit_24bargraph shiftlight1 = Adafruit_24bargraph(&i2c); // first shift light
Adafruit_24bargraph shiftlight2 = Adafruit_24bargraph(&i2c); // second shift l ight
TextLCD_I2C lcd(&i2c, 0x40, TextLCD::LCD20x4); // I2C bus, PCF8574 Slaveaddress, LCD Type


void CalcSpeed_ISR() {          //triggered every speed signal rising edge 
    int speedPeriod = speedPulseTimer.read_us();    // Get time since last interrupt  
    if( speedPeriod > 490000 ) g_vspeed = 0.0f;
    else if( speedPeriod < 2450 ) g_vspeed = 200.0f;
    else g_vspeed = 6313.13f*tireCirc/speedPeriod;    //converts period in us to speed (MPH)
    speedPulseTimer.reset();  
}


void CalcRPM_ISR() {            //triggered every rpm signal rising edge
    float rpm;
    static float oldrpm;        //static to keep value around for next time
    int rpmPeriod = rpmPulseTimer.read_us();    // Get time since last interrupt
    if( rpmPeriod > 20000000 ) rpm = 0;
    else if( rpmPeriod < 2000 ) rpm = 10000;
    else rpm = 20000000/rpmPeriod;            //converts period in us to RPM
    rpm = oldrpm+0.1586f*(rpm-oldrpm); // LP filter tuned to 0.3hz based on 10hz sample rate
    oldrpm = rpm;
    g_rpm = (int)rpm;
    rpmPulseTimer.reset();                      // Reset timer and wait for next interrupt
}


void SampleData_ISR() {     //called every sample rate
    g_sampleDataFlag = 1;
}


void ButtonCheck_ISR(){           
    static uint16_t state_btn1 = 0; // current debounce status
    static uint16_t state_btn2 = 0;
    static uint16_t state_rec = 0; 
    
    state_btn1 = ( state_btn1 << 1 ) | btn_1 | 0xE000; //select values?
    if( state_btn1 == 0xF000 ){ 
        g_menustate--;
        if( g_menustate < 0 ) g_menustate=6;
    }
    
    state_btn2 = ( state_btn2 << 1 ) | btn_2 | 0xE000; //increment screens
    if( state_btn2 == 0xF000 ){ 
        g_menustate++;
        if( g_menustate > 6 ) g_menustate=0;
    }
    
    state_rec = ( state_rec << 1 ) | btn_rec | 0xE000; //toggle recording
    if( state_rec == 0xF000 ) {
        if(g_menustate == 3){ //if gforce screen
            gforcepk.x = 0;
            gforcepk.y = 0;
            gforcepk.z = 0;   
        }
        else
            g_isLogging = !g_isLogging;
    }
}


void gps_ISR(){     // GPS Buffer 
    char c = gps.getc(); //Read the value out of the UART buffer
    nmea.fusedata(c);
}



/************
 *** MAIN ***
 ************/
int main() {
    
    bool wasLogging = false;
    int fileNumber = 0;
    char fname[16];

    // set baud rate for UART over USB to PC
    pc.baud(115200);
    
    // config sensors
    sensor[0].type = 'T';
    strncpy(sensor[0].name, "WTR T", 5);sensor[0].name[5] = '\0';
    sensor[0].alarmmin = 30;
    sensor[0].alarmmax = 210;
    sensor[0].graphmin = 120;
    sensor[0].graphmax = 240;
    sensor[0].valuemin = 50000;
    sensor[0].valuemax = -50000;
    sensor[0].alarmstate = 'N';

    sensor[1].type = 'T';
    strncpy(sensor[1].name, "OIL T", 5);sensor[1].name[5] = '\0';
    sensor[1].alarmmin = 30;
    sensor[1].alarmmax = 230;
    sensor[1].graphmin = 140;
    sensor[1].graphmax = 280;
    sensor[1].valuemin = 50000;
    sensor[1].valuemax = -50000;
    sensor[1].alarmstate = 'N';

    sensor[2].type = 'X';
    strncpy(sensor[2].name, "CHAN3", 5);sensor[2].name[5] = '\0';
    sensor[2].alarmmin = 0;
    sensor[2].alarmmax = 4096;
    sensor[2].valuemin = 50000;
    sensor[2].valuemax = -50000;
    sensor[2].alarmstate = 'N';

    sensor[3].type = 'X';
    strncpy(sensor[3].name, "CHAN4", 5);sensor[3].name[5] = '\0';
    sensor[3].alarmmin = 0;
    sensor[3].alarmmax = 4096;
    sensor[3].valuemin = 50000;
    sensor[3].valuemax = -50000;
    sensor[3].alarmstate = 'N';
    
    sensor[4].type = 'P';
    strncpy(sensor[4].name, "OIL P", 5);sensor[4].name[5] = '\0';
    sensor[4].alarmmin = 10;
    sensor[4].alarmmax = 90;
    sensor[4].graphmin = 0;
    sensor[4].graphmax = 100;
    sensor[4].valuemin = 50000;
    sensor[4].valuemax = -50000;
    sensor[4].alarmstate = 'N';
    
    sensor[5].type = '%';
    strncpy(sensor[5].name, "  TPS", 5);sensor[5].name[5] = '\0';
    sensor[5].alarmmin = -10;
    sensor[5].alarmmax = 110;
    sensor[5].graphmin = 0;
    sensor[5].graphmax = 100;
    sensor[5].valuemin = 50000;
    sensor[5].valuemax = -50000;
    sensor[5].alarmstate = 'N';
    
    sensor[6].type = 'X';
    strncpy(sensor[6].name, "CHAN7", 5);sensor[6].name[5] = '\0';
    sensor[6].alarmmin = 0;
    sensor[6].alarmmax = 4096;
    sensor[6].valuemin = 50000;
    sensor[6].valuemax = -50000;
    sensor[6].alarmstate = 'N';
    
    sensor[7].type = 'X';
    strncpy(sensor[7].name, "CHAN8", 5);sensor[7].name[5] = '\0';
    sensor[7].alarmmin = 0;
    sensor[7].alarmmax = 4096;
    sensor[7].valuemin = 50000;
    sensor[7].valuemax = -50000;
    sensor[7].alarmstate = 'N';
                       
    // turn off LEDs
    led1 = 1;
    led2 = 1;
    led3 = 0;
    led4 = 0;
    
    /*** Setup i2c ***/
    i2c.frequency(1000000); //LCD, shiftlight, accelerometer (400k)
    
    /* Setup ADC and SPI bus */
    DisplayLine(0,"                    ");
    DisplayLine(1,"  Initializing...   ");
    DisplayLine(2,"  ADC               ");
    DisplayLine(3,"                    ");
    printf("Initializing ADC...\n");
    spi1.format(8,0);
    spi1.frequency(1000000);
    wait_ms(100);
    
    /*** Setup Shift Light ***/
    DisplayLine(0,"                    ");   
    DisplayLine(1,"  Initializing...   ");
    DisplayLine(2,"  Shift Light       ");
    DisplayLine(3,"                    ");
    printf("Initializing Shift Light...\n");
    shiftlight1.begin(shiftAddr1);
    shiftlight2.begin(shiftAddr2);
    wait_ms(100);
    
    /*** Setup Accelerometer */
    DisplayLine(0,"                    ");
    DisplayLine(1,"  Initializing...   ");
    DisplayLine(2,"  Accelerometer     ");
    DisplayLine(3,"                    ");
    printf("Initializing Accelerometer...\n");
    if(!accel.setRange(MMA7455::Range_2g)) {
        printf("Unable to set range for MMA7455!\n");
    }
    wait_ms(50);
    if (!accel.setMode(MMA7455::ModeMeasurement)) {
        printf("Unable to set mode for MMA7455!\n");
    }
    wait_ms(50);
    if (!accel.calibrate()) {
        printf("Failed to calibrate MMA7455!\n");
    }
    wait_ms(50);
    
    /*** Setup RPM pulse timer ***/
    //rpmIntInput.mode(PullDown);             // Set the pin to Pull Down mode. REMEMBER TO SWITCH
    rpmIntInput.rise(&CalcRPM_ISR);         // Set up the interrupt for rising edge
    rpmPulseTimer.start();                  // start the timer
    
    /*** Setup Speed pulse timer ***/
    //speedIntInput.mode(PullDown);           // Set the pin to Pull Down mode.
    speedIntInput.rise(&CalcSpeed_ISR);     // Set up the interrupt for rising edge
    speedPulseTimer.start();    
    
    // Setup the GPS
    DisplayLine(0,"                    ");
    DisplayLine(1,"  Initializing...   ");
    DisplayLine(2,"  GPS               ");
    DisplayLine(3,"                    ");
    printf("Initializing GPS...\n");
    gps.baud(115200);
    wait_ms(100);
    //gps.printf("$PMTK220,1000*1F\r\n"); //1hz
    gps.printf("$PMTK220,200*2C\r\n"); //5hz
    //gps.printf("$PMTK220,100*2F\r\n"); // 10hz
    wait_ms(100);
    gps.printf("$PMTK314,0,1,0,1,0,0,0,0,0,0,0,0,0,0,0,0,0,0,0*28\r\n"); // GGA and RMC
    wait_ms(100);
    gps.printf("$PMTK313,1*2E\r\n"); //enable SBAS mode
    wait_ms(100);
    gps.printf("$PMTK301,2*2E\r\n"); //set DGPS/SBAS to WAAS mode
    wait_ms(100);
    gps.printf("$PMTK397,0*23\r\n"); //disable nav speed threshold
    wait_ms(100);
    gps.attach(&gps_ISR);
    wait_ms(100);
    
    /* Setup LCD */
    lcd.setUDC(0, (char *) udc_bar_1);    
    lcd.setUDC(1, (char *) udc_bar_2);    
    lcd.setUDC(2, (char *) udc_bar_3);   
    lcd.setUDC(3, (char *) udc_bar_4);   
    lcd.setUDC(4, (char *) udc_bar_5);  
    lcd.setUDC(5, (char *) udc_tophalf); 
    lcd.setUDC(6, (char *) udc_bothalf); 
    lcd.setUDC(7, (char *) udc_fullblock); //same as putc(255);
    lcd.cls();
    
    /*** SD Card Setup ***/
    DisplayLine(0,"                    ");
    DisplayLine(1,"  Initializing...   ");
    DisplayLine(2,"  SD Card           ");
    DisplayLine(3,"                    ");
    printf("Initializing SD Card...\n");
    wait_ms(100);
    FILE *fp;
    if(!mcifs.cardInserted()) {
        printf("Please insert a SD/MMC card\n");
        DisplayLine(0,"                    ");
        DisplayLine(1,"    NO SD CARD!!!   ");
        DisplayLine(2,"                    ");
        DisplayLine(3,"                    ");
        wait(3);
    }
    else{
        printf("Found SD/MMC card\n");
        DisplayLine(0,"                    ");
        DisplayLine(1,"SD Card OK          ");
        DisplayLine(2,"                    ");
        DisplayLine(3,"                    ");
        wait_ms(100);
    }
    
    /* Init Screen */
    DisplayLine(0,"                    ");   
    DisplayLine(1," Digital Dashboard  ");
    DisplayLine(2,"    V1.02 2015      ");
    DisplayLine(3,"                    ");
    printf("Digital Dashboard V1.02\n");
    wait_ms(750);
    lcd.cls();
    
    /*** Setup and Start Button Checking Ticker ***/
    twohundredHzTicker.attach(&ButtonCheck_ISR, 0.005); //buttons are checked every 5ms
    
    /*** Setup and Start Sampling Ticker ***/
    tenHzTicker.attach(&SampleData_ISR, 0.1); //10hz data is sampled once every 0.1s
    
    // MAIN LOOP //
    while(1) {
             
        if( g_rpm < 1000 ){
            logtimeouttimer.reset();
            logtimeouttimer.start();
        }     
             
        if( logtimeouttimer.read() > 10 ) //greater than 10s
            g_isLogging = false;
             
        if( g_sampleDataFlag == 1 ) { //time to sample!
            
            led1 = 0; //turn on
            
            /*** Get GPS data ***/
            GetGPSData();
                   
            /*** Sample 16 ADC Channels ***/ 
            GetADCData();
            
            /*** Get Accelerometer Data ***/
            GetAccelData();
               
            /*** Get Gear Selected ***/
            CalcGear();


            /*** Display Shift Light ***/
            DisplayShiftLight(3000, redline);

            /*** Display Dashboard ***/
            DisplayDash();
            
            
            /*** write to SD Card ***/
            if( g_isLogging ){    //printf("logging enabled\n\r");           
                if( mcifs.cardInserted() ){ //check for SD card              
                    if( wasLogging ){ //continuing to log  //printf("continuing to log\n\r");  
                                    //Time,Longi ,Lati  ,Altit,GPSu,X    ,Y    ,MPH  ,Heading,RPM ,Gear,WT   ,OT   ,OP   ,TPS\n");
                        fprintf(fp, "%9.3f,%10.6f,%10.6f,%8.2f,%10d,%6.3f,%6.3f,%5.1f,%7.1f,%4d,%4d,%5.1f,%5.1f,%5.1f,%3d\n",logtimer.read(),gps_long,gps_lat,gps_alt,1,gforce.x,gforce.y,g_vspeed,gps_head,g_rpm,g_gear,sensor[0].value, sensor[1].value, sensor[4].value, (int)sensor[5].value);                    
                    }
                    else{   //just enabled logging, setup file   //printf("open new file\n\r");
                        snprintf(fname,16,"/mci/datalog%04d.csv",fileNumber); // change to match your file name structure               
                        fp = fopen(fname,"r");        
                        while (fp) {    //search for latest file name
                          fclose(fp);
                          fileNumber++;
                          snprintf(fname,16,"/mci/datalog%04d.csv",fileNumber); //update filename to search
                          fp = fopen(fname,"r"); //checking existence of fname
                        }             
                        fp = fopen(fname, "w"); //current log file name
                        if (fp != NULL) {
                            fprintf(fp, "Time     ,Longitude ,Latitude  ,Altitude,GPS_update,X     ,Y     ,MPH  ,Heading,RPM ,Gear,WTR T,OIL T,OIL P,TPS\n");
                            //fprintf(fp, "12345.123,123.123456,123.123456,12345.12,         1,-1.123,-1.123,123.1,  127.1,1234,   1,123.1,123.1,123.1,123\n");
                            logtimer.reset();
                            logtimer.start();
                        } else {
                            printf("Failed to open log file\n");
                        }   
                    }
                }//else{ //SD card NOT inserted
                 //   lcd.printf("    NO SD CARD!!!   ");
                //}
            } // end of g_isLogging
            else if(wasLogging==true){
                 fclose(fp); //close file
            }
            
            wasLogging = g_isLogging; //save current state to previous   
            g_sampleDataFlag = 0;     
            led1 = 1;     //led off
        } //end of sampling, g_sampleDataFlag==1
        
    } //end of while(1)

} //end of main()

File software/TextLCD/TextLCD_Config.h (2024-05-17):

/* mbed TextLCD Library, for a 4-bit LCD based on HD44780
 * Copyright (c) 2014, WH
 *               2014, v01: WH, Extracted from TextLCD.h as of v14
 *               2014, v02: WH, Added AC780 support, added I2C expander modules, fixed setBacklight() for inverted logic modules. Fixed bug in LCD_SPI_N define
 *               2014, v03: WH, Added LCD_SPI_N_3_8 define for ST7070
 *
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
 * THE SOFTWARE IS PROVIDED "AS IS", WITHOUT WARRANTY OF ANY KIND, EXPRESS OR
 * IMPLIED, INCLUDING BUT NOT LIMITED TO THE WARRANTIES OF MERCHANTABILITY,
 * FITNESS FOR A PARTICULAR PURPOSE AND NONINFRINGEMENT. IN NO EVENT SHALL THE
 * AUTHORS OR COPYRIGHT HOLDERS BE LIABLE FOR ANY CLAIM, DAMAGES OR OTHER
 * LIABILITY, WHETHER IN AN ACTION OF CONTRACT, TORT OR OTHERWISE, ARISING FROM,
 * OUT OF OR IN CONNECTION WITH THE SOFTWARE OR THE USE OR OTHER DEALINGS IN
 * THE SOFTWARE.
 */
#ifndef MBED_TEXTLCDCONFIG_H
#define MBED_TEXTLCDCONFIG_H

//Select hardware interface options to reduce memory footprint (multiple options allowed)
#define LCD_I2C        1           /* I2C Expander PCF8574/MCP23008 */
#define LCD_SPI        0           /* SPI Expander SN74595          */
#define LCD_I2C_N      0           /* Native I2C bus     */
#define LCD_SPI_N      0           /* Native SPI bus     */
#define LCD_SPI_N_3_8  0           /* Native SPI bus     */
#define LCD_SPI_N_3_9  0           /* Native SPI bus     */
#define LCD_SPI_N_3_10 0           /* Native SPI bus     */
#define LCD_SPI_N_3_16 0           /* Native SPI bus     */
#define LCD_SPI_N_3_24 0           /* Native SPI bus     */

//Select options to reduce memory footprint (multiple options allowed)
#define LCD_UDC        1           /* Enable predefined UDC example*/                
#define LCD_PRINTF     1           /* Enable Stream implementation */                

//Pin Defines for I2C PCF8574/PCF8574A or MCP23008 and SPI 74595 bus expander interfaces
//LCD and serial portexpanders should be wired accordingly 
//
//Select Hardware module (one option only)
#define DEFAULT        0
#define ADAFRUIT       1
#define DFROBOT        0
#define YWROBOT        0
#define GYLCD          0
#define SYDZ           0

//Select Hardware module (one option only)
#if (DEFAULT==1)
//Definitions for default (WH) mapping between serial port expander pins and LCD controller
//This hardware supports the I2C bus expander (PCF8574/PCF8574A or MCP23008) and SPI bus expander (74595) interfaces
//See https://mbed.org/cookbook/Text-LCD-Enhanced
//
//Note: LCD RW pin must be connected to GND
//      E2 is used for LCD40x4 (second controller)
//      BL may be used to control backlight
#define D_LCD_PIN_D4   0
#define D_LCD_PIN_D5   1
#define D_LCD_PIN_D6   2
#define D_LCD_PIN_D7   3
#define D_LCD_PIN_RS   4
#define D_LCD_PIN_E    5
#define D_LCD_PIN_E2   6
#define D_LCD_PIN_BL   7

#define D_LCD_PIN_RW   D_LCD_PIN_E2

//Select I2C Portexpander type (one option only)
#define PCF8574        1
#define MCP23008       0

//Inverted Backlight control
#define BACKLIGHT_INV  0
#endif

#if (ADAFRUIT==1)
//Definitions for Adafruit i2cspilcdbackpack mapping between serial port expander pins and LCD controller
//This hardware supports both an I2C expander (MCP23008) and an SPI expander (74595) selectable by a jumper.
//Slaveaddress may be set by solderbridges (default 0x40). SDA/SCL has pullup Resistors onboard.
//See http://www.ladyada.net/products/i2cspilcdbackpack
//
//Note: LCD RW pin must be kept LOW
//      E2 is not available on this hardware and so it does not support LCD40x4 (second controller)
//      BL is used to control backlight
#define D_LCD_PIN_0    0
#define D_LCD_PIN_RS   1
#define D_LCD_PIN_E    2
#define D_LCD_PIN_D4   3
#define D_LCD_PIN_D5   4
#define D_LCD_PIN_D6   5
#define D_LCD_PIN_D7   6
#define D_LCD_PIN_BL   7

#define D_LCD_PIN_E2   D_LCD_PIN_0

//Force I2C portexpander type
#define PCF8574        0
#define MCP23008       1

//Inverted Backlight control
#define BACKLIGHT_INV  0
#endif

#if (DFROBOT==1)
//Definitions for DFROBOT LCD2004 Module mapping between serial port expander pins and LCD controller
//This hardware uses PCF8574 and is different from earlier/different Arduino I2C LCD displays
//Slaveaddress hardwired to 0x4E. SDA/SCL has pullup Resistors onboard.
//See http://arduino-info.wikispaces.com/LCD-Blue-I2C
//
//Definitions for DFROBOT V1.1 
//This hardware uses PCF8574. Slaveaddress may be set by jumpers (default 0x40).
//SDA/SCL has pullup Resistors onboard and features a voltage level converter 3V3 <-> 5V.
//See http://www.dfrobot.com/index.php?route=product/product&product_id=135
//
//
//Note: LCD RW pin must be kept LOW
//      E2 is not available on default Arduino hardware and so it does not support LCD40x4 (second controller)
//      BL is used to control backlight
#define D_LCD_PIN_RS   0
#define D_LCD_PIN_RW   1
#define D_LCD_PIN_E    2
#define D_LCD_PIN_BL   3
#define D_LCD_PIN_D4   4
#define D_LCD_PIN_D5   5
#define D_LCD_PIN_D6   6
#define D_LCD_PIN_D7   7
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

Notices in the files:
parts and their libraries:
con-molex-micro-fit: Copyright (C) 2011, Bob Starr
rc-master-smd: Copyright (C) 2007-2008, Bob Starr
